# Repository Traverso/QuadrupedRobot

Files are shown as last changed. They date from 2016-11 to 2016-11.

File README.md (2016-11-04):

#Felix - a 3D Printable Quadruped Robot
-----------------------------------------
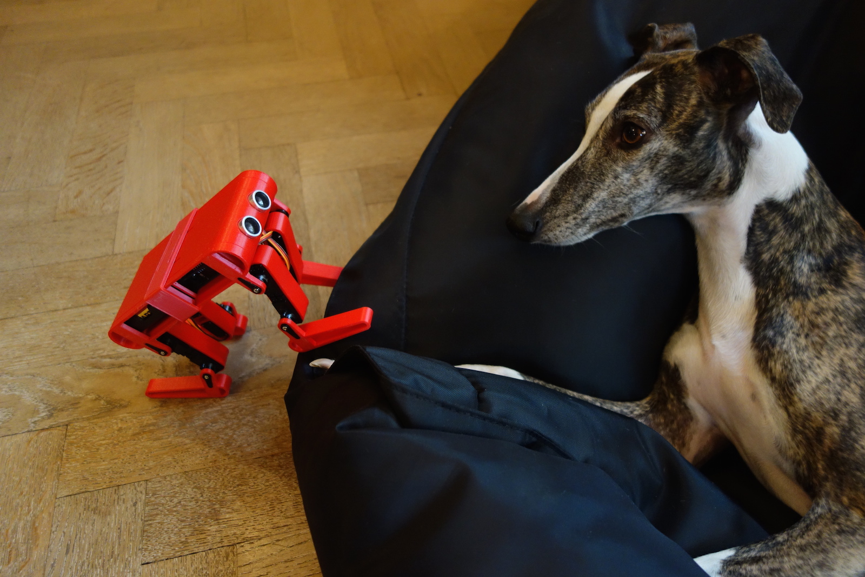
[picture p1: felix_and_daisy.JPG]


Simple 3D printable quadruped robot,
driven by 8 servos and a microcontroller.

For information on how to assemble, integrate the electronics
and program the robot to walk, visit:

www.burningservos.com

If you build your own version of Felix I'll appreciate if you tweet me
a picture @RonaldXJT  =)

## License
Copyright (c) 2016 Ronald Jaramillo <ronald@burningservos.com> @RonaldXJT
Licensed under the MIT license.

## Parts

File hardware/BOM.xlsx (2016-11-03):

Quantity | Item | URL | price (USD)
1 | 8-Channel PWM or Servo FeatherWing Add-on For All Feather Boards PID: 2928 | https://www.adafruit.com/products/2928 | 9.95
1 | Adafruit Feather M0 Bluefruit LE PID: 2995 | https://www.adafruit.com/products/2995 | 29.95
1 | Lithium Ion Polymer Battery - 3.7v 150mAh PID: 1317 | https://www.adafruit.com/products/1317 | 5.95
1 | 4 x AA Battery Holder with On/Off Switch PID: 830 | https://www.adafruit.com/products/830 | 2.95
1 | 3x4 Right Angle Male Header - 4 pack PID: 816 | https://www.adafruit.com/products/816 | 2.95
1 | Feather Header Kit - 12-pin and 16-pin Female Header Set PID: 2886 | https://www.adafruit.com/products/2886 | 0.95
1 | Feather Stacking Headers - 12-pin and 16-pin female headers PID: 2830 | https://www.adafruit.com/products/2830 | 1.25
8 | Micro Servo - MG90S High Torque Metal Gear PID: 1143 | https://www.adafruit.com/products/1143 | 79.60
2 | Mini Panel Mount DPDT Toggle Switch PID: 3220 | https://www.adafruit.com/products/3220 | 2.50
 |  | Total: | 136.05

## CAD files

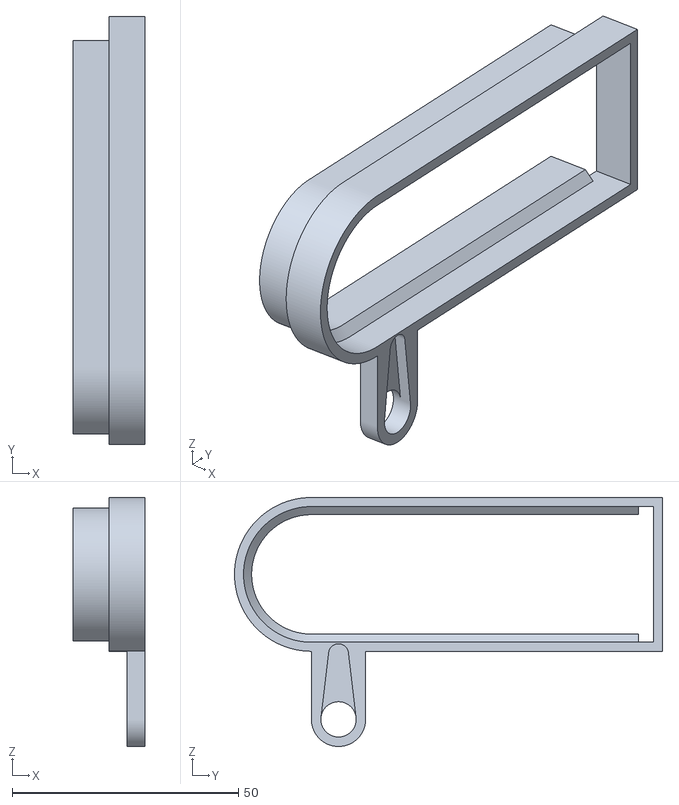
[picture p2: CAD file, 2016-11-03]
hardware/STL_3D_files/HipFrontRight.stl
16.0 x 94.6 x 55.0

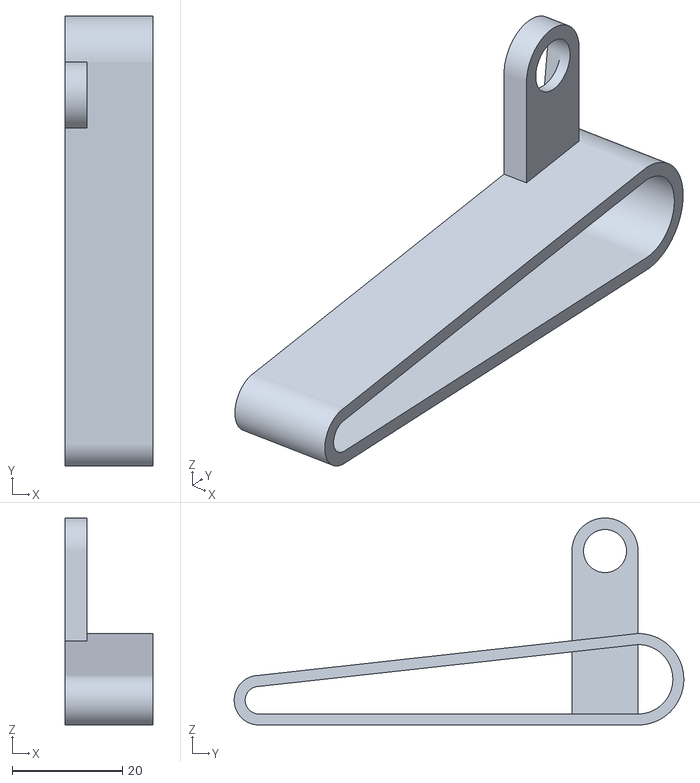
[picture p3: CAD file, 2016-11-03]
hardware/STL_3D_files/TibiaFrontLeft.stl
16.0 x 81.6 x 37.6

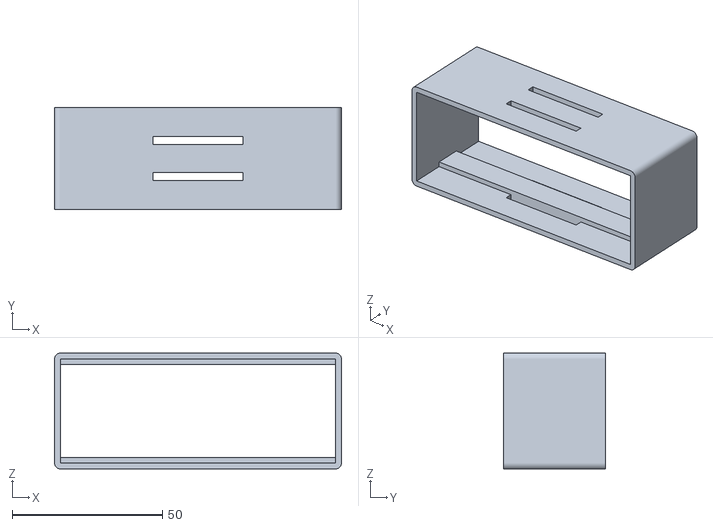
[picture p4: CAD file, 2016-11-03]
hardware/STL_3D_files/Belt.stl
95.6 x 34.0 x 38.6

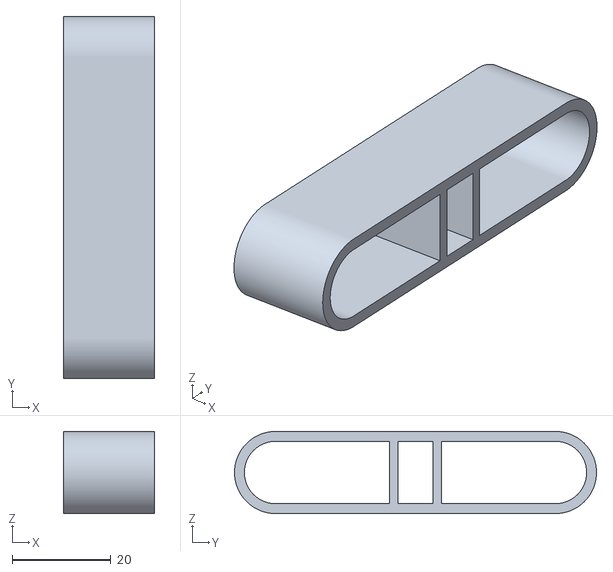
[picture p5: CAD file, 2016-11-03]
hardware/STL_3D_files/FemurFrontRight.stl
18.5 x 73.2 x 16.6

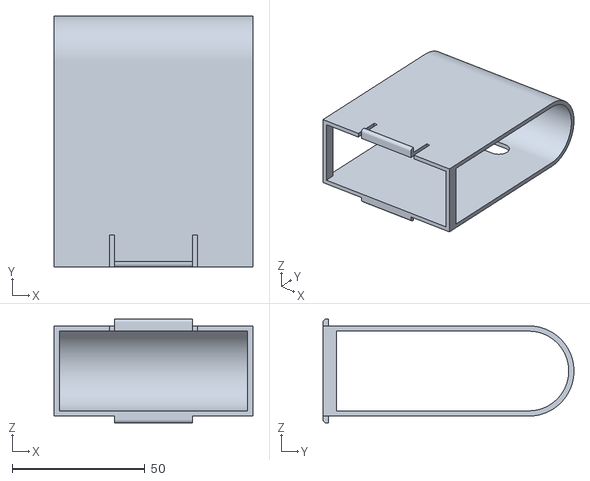
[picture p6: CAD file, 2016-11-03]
hardware/STL_3D_files/BodyBack.stl
75.0 x 94.6 x 39.2

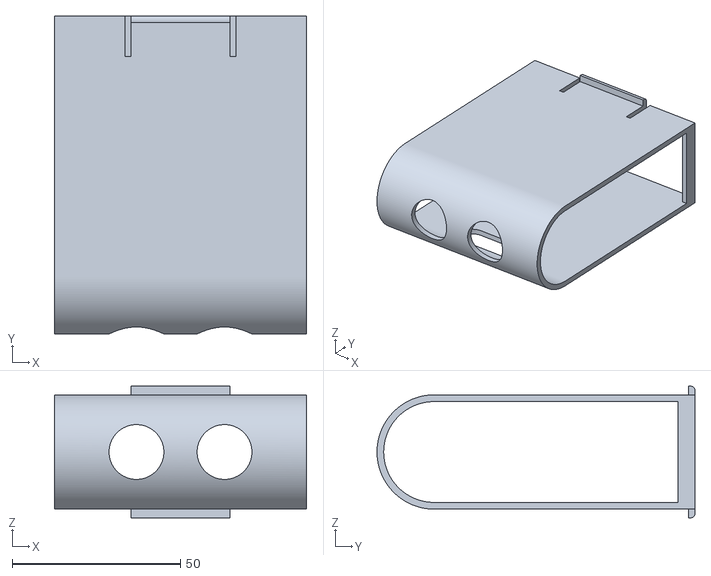
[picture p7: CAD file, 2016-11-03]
hardware/STL_3D_files/BodyFront.stl
75.0 x 94.6 x 39.2

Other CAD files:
hardware/STL_3D_files/HipBackLeft.stl
hardware/STL_3D_files/TibiaBackLeft.stl
hardware/STL_3D_files/TibiaFrontRight.stl
hardware/STL_3D_files/FemurBackLeft.stl
hardware/STL_3D_files/FemurBackRight.stl
hardware/STL_3D_files/FemurFrontLeft.stl
hardware/STL_3D_files/HipBackRight.stl
hardware/STL_3D_files/TibiaBackRight.stl
hardware/STL_3D_files/HipFrontLeft.stl

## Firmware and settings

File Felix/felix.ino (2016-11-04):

/*************************************************** 
 Felix Quadruped Robot
 Version:2.0
 Author: Ronald Jaramillo @RonaldXJT
 Web: www.burningservos.com
 ****************************************************/
#include <Wire.h>
#include <string.h>
#include <Arduino.h>
#include <SPI.h>
#include <Adafruit_PWMServoDriver.h>

#include "Adafruit_BLE.h"
#include "Adafruit_BluefruitLE_SPI.h"
#include "Adafruit_BluefruitLE_UART.h"
#include "includes.h"


Adafruit_BluefruitLE_SPI ble(BLUEFRUIT_SPI_CS, BLUEFRUIT_SPI_IRQ, BLUEFRUIT_SPI_RST);


void setup() {
  while(!Serial);  
  delay(500);
  
  Serial.begin(115200);
  Serial.println("Felix V2.0");

  legSetup();
  homePosition();

  //calibrate();
  //return;
  
 
  communicationSetup();
  controllerSetup();

  
  loadWalk(CURRENT_WALK,CURRENT_STEP_COUNT,MOVING_FORWARD,0);


}


void loop() {

  if(runController())
  {
      controllerLoop();
  }
  else
  {
    communicationLoop();
  }

}

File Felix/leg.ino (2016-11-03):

/**
 * legSetup
 * Initialize legs and servos
 */
void legSetup()
{
  pwm.begin();
  pwm.setPWMFreq(60);  
  
  for(int i = 0; i < LEGS_COUNT; i++)
  {
    leg lg;
    lg.idx = i;
    LEGS[i] = lg;
  }
}

/**
 * homePosition
 * Move legs to default "ready" position
 */
void homePosition()
{
  for(int i = 0; i < LEGS_COUNT; i++)
  {
    moveTo(i, { POSE_ORIGIN_X, POSE_ORIGIN_Y });
  }
}

/**
 * calibrate
 * Move all servos to 90 degrees (incluede delta/slack)
 * to control leg angles 
 */
void calibrate()
{
  for(int i = 0; i < LEGS_COUNT; i++)
  {
    calibrateLeg(i);
  }
}
void calibrateLeg(int leg)
{
    Serial.print("calibrating leg:");
    Serial.println(leg);
    
    pwm.setPWM(SERVOS[leg][0],0,map(90 + SERVO_SLACK[leg][0], 0, 180, SERVOMIN, SERVOMAX));
    pwm.setPWM(SERVOS[leg][1],0,map(90 + SERVO_SLACK[leg][1], 0, 180, SERVOMIN, SERVOMAX));
}

void pin(int leg, struct point from, struct point to, bool append)
{
  int radX= radiusX(from.x,to.x);
  int cx = midPointX(radX,from.x,to.x); 

  struct arc ac;
  ac.origin = { cx, to.y };
  ac.radius = { radX,PIN_HEIGHT };

  ac.start_angle = 360;
  ac.end_angle = 180;

  /*
  if(shouldMirrow(leg))
  {
    ac.start_angle = 180;
    ac.end_angle = 360;
  }*/

  /*
  Serial.print("radx:");
  Serial.print(radX);
  Serial.print(", cx:");
  Serial.println(cx);
  */

  ellipticalTrajectoryForLeg(ac, &LEGS[leg], append, (to.x > from.x) );
  
  registerTrajectory(leg);
}

int midPointX(int cx, int x1, int x2) 
{
  return (x1 > x2)? x2 + cx: x1 + cx;
}

int radiusX(int x1, int x2)
{
  float cx = (x1 > x2)? x1 - x2: x2 - x1;
  cx = cx  / 2;
  int cx_ = (int) cx;
  return cx_;
}

/**
 * drag
 * Calculate the linear trajectory from the current x to the requested position
 * register the leg for moving 
 *
 * @param int leg  - index to the active leg
 * @param struct point p  - where to drag to
 */
void drag(int leg, struct point from, struct point to, bool append)
{
  struct line ln;
  ln.P1 = from;
  ln.P2 = to;
  linearTrajectoryForLeg(ln,&LEGS[leg], append);
  
  //reg for moving...
  registerTrajectory(leg);
}

/***************************************************
 * Given a requested endpoint find the joint angles and pass the values to the serovs
 * @param struct line ln - line to lerp
 * @param struct leg L - leg reference to setup trajectory 
****************************************************/
void ellipticalTrajectoryForLeg(struct arc ac, struct leg *L, bool append, bool reverse)
{
    float step_size = (ac.end_angle - ac.start_angle) / SAMPLING_GRANULARITY;
    int c_angle = ac.start_angle;
    c_angle += step_size;

    if(!append) L->trajectory_length = 0;

    int n = SAMPLING_GRANULARITY;
    for(int i = 0; i < SAMPLING_GRANULARITY; i++)
    {
        float x = ac.origin.x + ac.radius.x * cos(c_angle/RAD_TO_DEG);
        float y = ac.origin.y + ac.radius.y * sin(c_angle/RAD_TO_DEG);

        int x_ = (int) x;
        int y_ = (int) y;
        struct point p = { x_, y_ };

        n--;
        int dir = (reverse)? n:i;
        int idx = L->trajectory_length + dir;
        L->trajectory[idx] = p; 

        c_angle+= step_size; 
    }
    L->trajectory_length += SAMPLING_GRANULARITY;
}

/***************************************************
 * Given a requested endpoint find the joint angles and pass the values to the serovs
 * @param struct line ln - line to lerp
 * @param struct leg L - leg reference to setup trajectory 
****************************************************/
void linearTrajectoryForLeg(struct line ln, struct leg *L, bool append)
{
    //find the slope/delta
    float delta_x = ln.P2.x - ln.P1.x;
    float delta_y = ln.P2.y - ln.P1.y;

    //clear the trajectory
    if(!append) L->trajectory_length = 0;

    float distance = sqrt( ((delta_x) * (delta_x)) + ((delta_y) * (delta_y)) );

    if(distance < 1) return;

    //divide the line int the required number of points
    float step_size = distance / SAMPLING_GRANULARITY;
    float current_step = step_size; //skip the first point 

    
    for(int i = 0; i < SAMPLING_GRANULARITY; i++)
    {
       float increment = current_step / distance;
       float x = ln.P1.x + (increment * delta_x);
       float y = ln.P1.y + (increment * delta_y);

       int x_ = (int) x;
       int y_ = (int) y;
       struct point p = { x_, y_ };

       L->trajectory[L->trajectory_length + i] = p; 

       current_step += step_size;
    }

    L->trajectory_length += SAMPLING_GRANULARITY;
}

/***************************************************
 * Given a requested endpoint find the joint angles and pass the values to the serovs
 * @param int leg - index to leg
 * @param struct point p - requested position of endpoint
 **************************************************/
void moveTo(int leg, struct point p)
{
  pose po = IK(FEMUR_SIZE,TIBIA_SIZE,p);  
  if(shouldMirrow(leg))
  {
     po.hip_angle = 180 - po.hip_angle; 
     po.knee_angle = 180 - po.knee_angle;
  }
  setRotationAngles(leg, po.hip_angle, po.knee_angle);
}

bool shouldMirrow(int leg)
{
  return (leg == BACK_RIGHT || leg == FRONT_LEFT);
}

/***************************************************
 * Command the rotation angle of the hip and knee to the servos
 * @param int leg - index to leg
 * @param int hip - hip angle
 * @param int knee - knee angle
 ***************************************************/
void setRotationAngles(int leg, int hip, int knee)
{
  int h = hip + SERVO_SLACK[leg][0];
  int k = knee + SERVO_SLACK[leg][1];

  pwm.setPWM(SERVOS[leg][0],0,map(h, 0, 180, SERVOMIN, SERVOMAX));
  pwm.setPWM(SERVOS[leg][1],0,map(k, 0, 180, SERVOMIN, SERVOMAX));

}
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
